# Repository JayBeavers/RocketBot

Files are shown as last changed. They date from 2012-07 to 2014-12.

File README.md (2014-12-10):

# RocketBot #


RocketBot is a project to create a robot that uses an air compressor to launch straw rockets that was demonstrated at the 2012 Maker Faires in San Mateo CA and Seattle WA.  Its journey is chronicalled at [http://jaybeavers.org](http://jaybeavers.org).

----------

## [RocketBaseArduino](https://github.com/JayBeavers/RocketBot/tree/master/RocketBaseArduino) ##

RocketBaseArduino is the source code for the Arduino that controls the robot platform that runs the rocket launcher which includes an air compressor, a pan/tilt servo for the launcher, an industrial LED warning light, and a warning speaker.

RocketBaseArduino is controlled using the [Reflecta](https://github.com/JayBeavers/Reflecta) remoting protocol.  RocketBaseArduino implements the 'RBOT1' interface which controls animations (lights and sounds), pan/tilt servos of the rocket launcher, and compressor and valves of the pneumatic system.  The PC receives a heartbeat of the current state of the robot every 200 ms.

The PC-side source code has not been published.  I've switched from a C#/XNA application to a [nodejs client](https://github.com/JayBeavers/Reflecta/tree/master/NodeClient) but the port is not yet complete.  The previous application used XBox Wireless Controller buttons to switch between animations and initiate launch and the thumb stick to drive the servos.

## [ReflectaMonsterMoto](https://github.com/JayBeavers/ReflectaMonsterMoto) ##

ReflectaMonsterMoto is the source code for the [Teensy (Arduino-compatible board)](http://www.pjrc.com/teensy/) and [SparkFun Monster Moto Shield](https://www.sparkfun.com/products/10182) system that runs the RocketBot drive train.

Like RocketBaseArduino, the PC-side source code has not been published due to a switch from C#/XNA over to nodejs.  The previous application used an XBox Wireless Controller thumbstick to control the drive train.  The logic behind this control was subject to much hacking over the course of Maker Faire as I adjusted the acceleration curve, turn rate, etc. to make the robot deftly controllable through the heavy crowds.

## [Schematics](https://github.com/JayBeavers/RocketBot/tree/master/Schematics) ##

I've uploaded the diagrams I used with a lasercutter to make the RocketBot plates.  There's also a layout of the pneumatic parts and an early draft of the power system used to enable the Arduino to control high current 12v components such as the compressor, industrial warning light, and pneumatic valves.

## [Parts List](https://github.com/JayBeavers/RocketBot/blob/master/PartsList.md) ##

List of parts used to create RocketBot.

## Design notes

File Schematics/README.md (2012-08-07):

# Hardware Schematics for RocketBot #

These are the design diagrams used to build the RocketBot prototype.

The base plate designs were created in Visio to be used on a laser cutter which had been tuned to work well with these settings (0 width lines, coloration for cut vs. raster).  These settings are different than what Ponoko wants so if you want to use that service to cut your plates some significant editing will be needed.

I loaded a few of these into AutoCAD 2013 (imports well) and InkScape (imports mostly intact).  I found Inkscape to do better with the SVG import than the dxf import so I've exported both formats.

The electronics design (.dsn file) was done using TinyCAD.  I didn't find an 'export to' in TinyCAD that was more portable so you'll need to use that app to read the file.

## Rocket Drive Base 4 ##

Base plate for the drive train for RocketBot.  I attached a Parallax drive train and two Parallax casters from an Eddie kit.  The empty front area held a Dell Mini-9 netbook running Windows 8, during the show we hotglued some straws to act as 'inside bumpers' to keep the netbook from sliding off the robot.  We added some zip ties and zip tie mounts to secure the battery.  We also found out the hard way that if you don't protect the Arduino's USB connector, hard use will strain and break the USB connection.

## Rocket Base 3 ##

Base plate for the rocket layer of RocketBot.  This was connected on top of Rocket Drive Base using the Eddie chassis spacers.  For the RTM release, we shifted the transistors down next to the air tank in order to shorten cable lengths.

We also found out the hard way that an Arduino mounted on the outside of the plate where the USB connector sticks out slightly is very bad -- at the end of the first day when I was quite tired I drove the robot into a pole on the left side and ripped off the USB connector, resulting in a hurried replacement of the Arduino from the Maker Shed.  RocketBot v2 has a laser cut 'cable holder' that takes all strain off the usb connectors.  I've also moved the Arduino (and all fragile components) inside the plate to get better crash protection.

## Rocket Electronics ##

This is a very simple diagram of the early circuits.  Much out of spec of what was finally produced.  Will rediagram for RocketBot v2.

## Pneumatic Prototype 1 ##

Layout of the pneumatic components.  In the final release I moved the analog pressure sensor to valve port 2 and removed the associated tee, otherwise pretty much unchanged.

## MARK 2 Drive Base v3 ##

A somewhat related project -- using most of the same components as RocketBot, add a centermount for an 8020 rod to make a 'human height' prototyping platform.  I did this work after seeing so many Parallax Eddies chopped up to remove their second platter and replace it with some type of height extension system.

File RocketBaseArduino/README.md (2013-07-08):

# Rocket Base Arduino #

Rocket Base Arduino exposes commands to allow a host to control the RocketBot's launch plate over the Arduino's USB or UART (Serial) port by using the Reflecta protocol via the rbot1 interface.

The commands exposed are:

- animation (id): Display a visual and audible animation sequence
    - 0: Idle
    - 1: Moving
    - 2: Arming
    - 3: Armed
    - 4: Firing
    - 5: Fired
    - 6: Moving Disabled
- fire(): Fire the rocket!
- light(val): Manually set the warning light LED bitmask (1:Red, 2:Green, 4: Blue)
- pan(angle)
- tilt(angle)
- compressor(on): '1' on, '0' off
- valve(val): '0' both off, '2' valve 2 open, '4' valve 4 open

In addition, pin A0 is hooked to the pressure sensor which can be accessed via ardu1.analogRead.

To install this library, upload sketch RocketBaseArduino to your Arduino.  Note that you must first [install the Reflecta Arduino libraries](https://github.com/JayBeavers/Reflecta#getting-started).

To call this library, use the [Reflecta Node Client](https://github.com/JayBeavers/Reflecta/tree/master/NodeClient) library.  A simple example is:

    var devicePath = "/dev/ttyACM0"; // or "COM4" et al in Windows
    var Reflecta = require('reflecta');
    var reflecta = new reflecta.Board(devicePath, function(err) {
      reflecta.rbot1.animation(4);
      reflecta.rbot1.fire();
      reflecta.rbot1.animation(5);
    });

## Release History

- 0.1.0: Initial release
- 0.1.1: Updated with changes to Reflecta and ardu1

### Future Work ###

- Convert custom heartbeat code over to Reflecta's new hart1 approach like in BasicIMU.ino
- Create an integrated nodejs sample that maps an XBox GamePad to these methods like was used at Maker Faire.
- To be reworked for Rocket Bot v2.

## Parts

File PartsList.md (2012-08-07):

# Parts List #

[Sparkfun Monster Moto Shield](https://www.sparkfun.com/products/10182), $80

2x [PJRC Teensy](http://www.pjrc.com/store/teensy.html) Arduino-compatible microcontroller, $16 ea

2x [Parallax Caster Wheel](http://www.parallax.com/Store/Robots/RoboticAccessories/tabid/145/CategoryID/22/List/0/SortField/0/Level/a/ProductID/527/Default.aspx) Kits, $43 ea

[Parallax Motor Mount and Wheel Kit](http://www.parallax.com/Store/Robots/RoboticAccessories/tabid/145/CategoryID/22/List/0/SortField/0/catpageindex/2/Level/a/ProductID/507/Default.aspx), $299

2x (45 cm x 45 cm x 1 cm) ABS plastic to cut bases, ~$12

[12.8V 6.6 Ah LiFePO4 Battery](http://www.batteryspace.com/LFP-Battery-12.8V-6.6Ah-84Wh-16A-rate-for-scuba-diving.aspx), $96

[Smart Battery Charger](http://www.batteryspace.com/smartcharger30afor128v4cellslifepo4batterypack110-240vac.aspx), $22

[FIRST 2012 Pneumatic Base Kit](http://www.andymark.com/product-p/am-2000.htm), $281

[Festo VUVG 12v Valve Pack](http://www.andymark.com/product-p/am-0888.htm), $94

[Menics MS86M Warning Light](http://www.wolfautomation.com/products/36249/86mm-led-strobe-light-3-colors-in-1brmenics-ms86m), $130

[Menics MS86 Pole Mount Adapter](http://www.wolfautomation.com/products/33066/pole-mount-adapterbrmenics-ms86-accessory-mam-ds31), $0

[Menics MAP Pole](http://www.wolfautomation.com/products/1029/poles-for-the-mam-basesbrmenics-map-pole), $5

[Servo City DDT500 Tilt](http://www.servocity.com/html/ddt500_direct_drive_tilt.html), $25

Copper launch tube & flexible tubing from local hardware store

Straws, Eraser tips, hot melt, and construction paper for rockets

Custom MOSFET power board

XBox Wireless Controller with PC Receiver

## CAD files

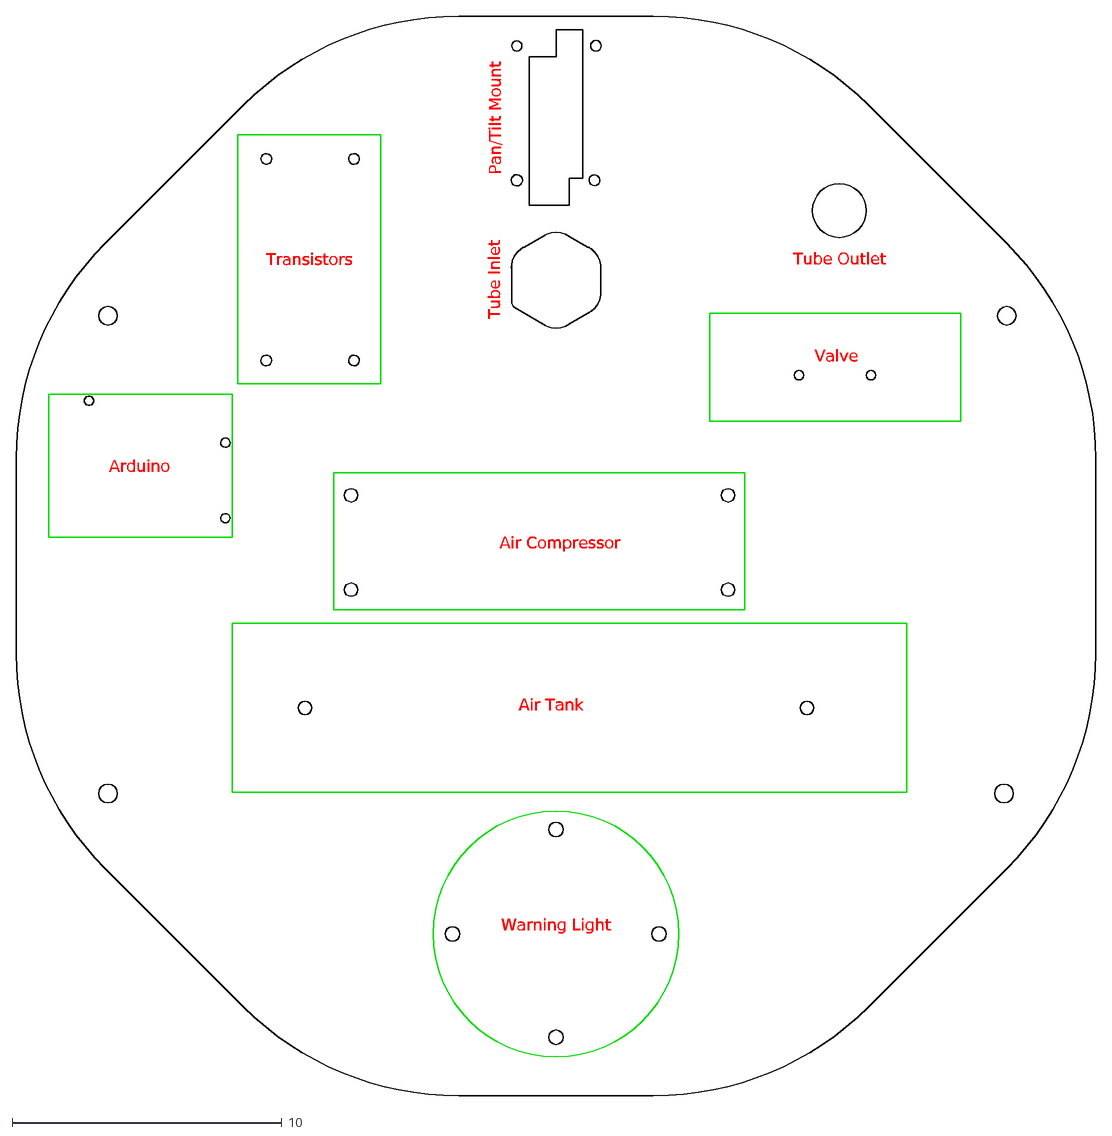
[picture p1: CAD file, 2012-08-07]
Schematics/Rocket Base 3.dxf
Pan/Tilt Mount
Tube Inlet
Air Compressor
Air Tank
Warning Light
Valve
Arduino
Transistors
Tube Outlet

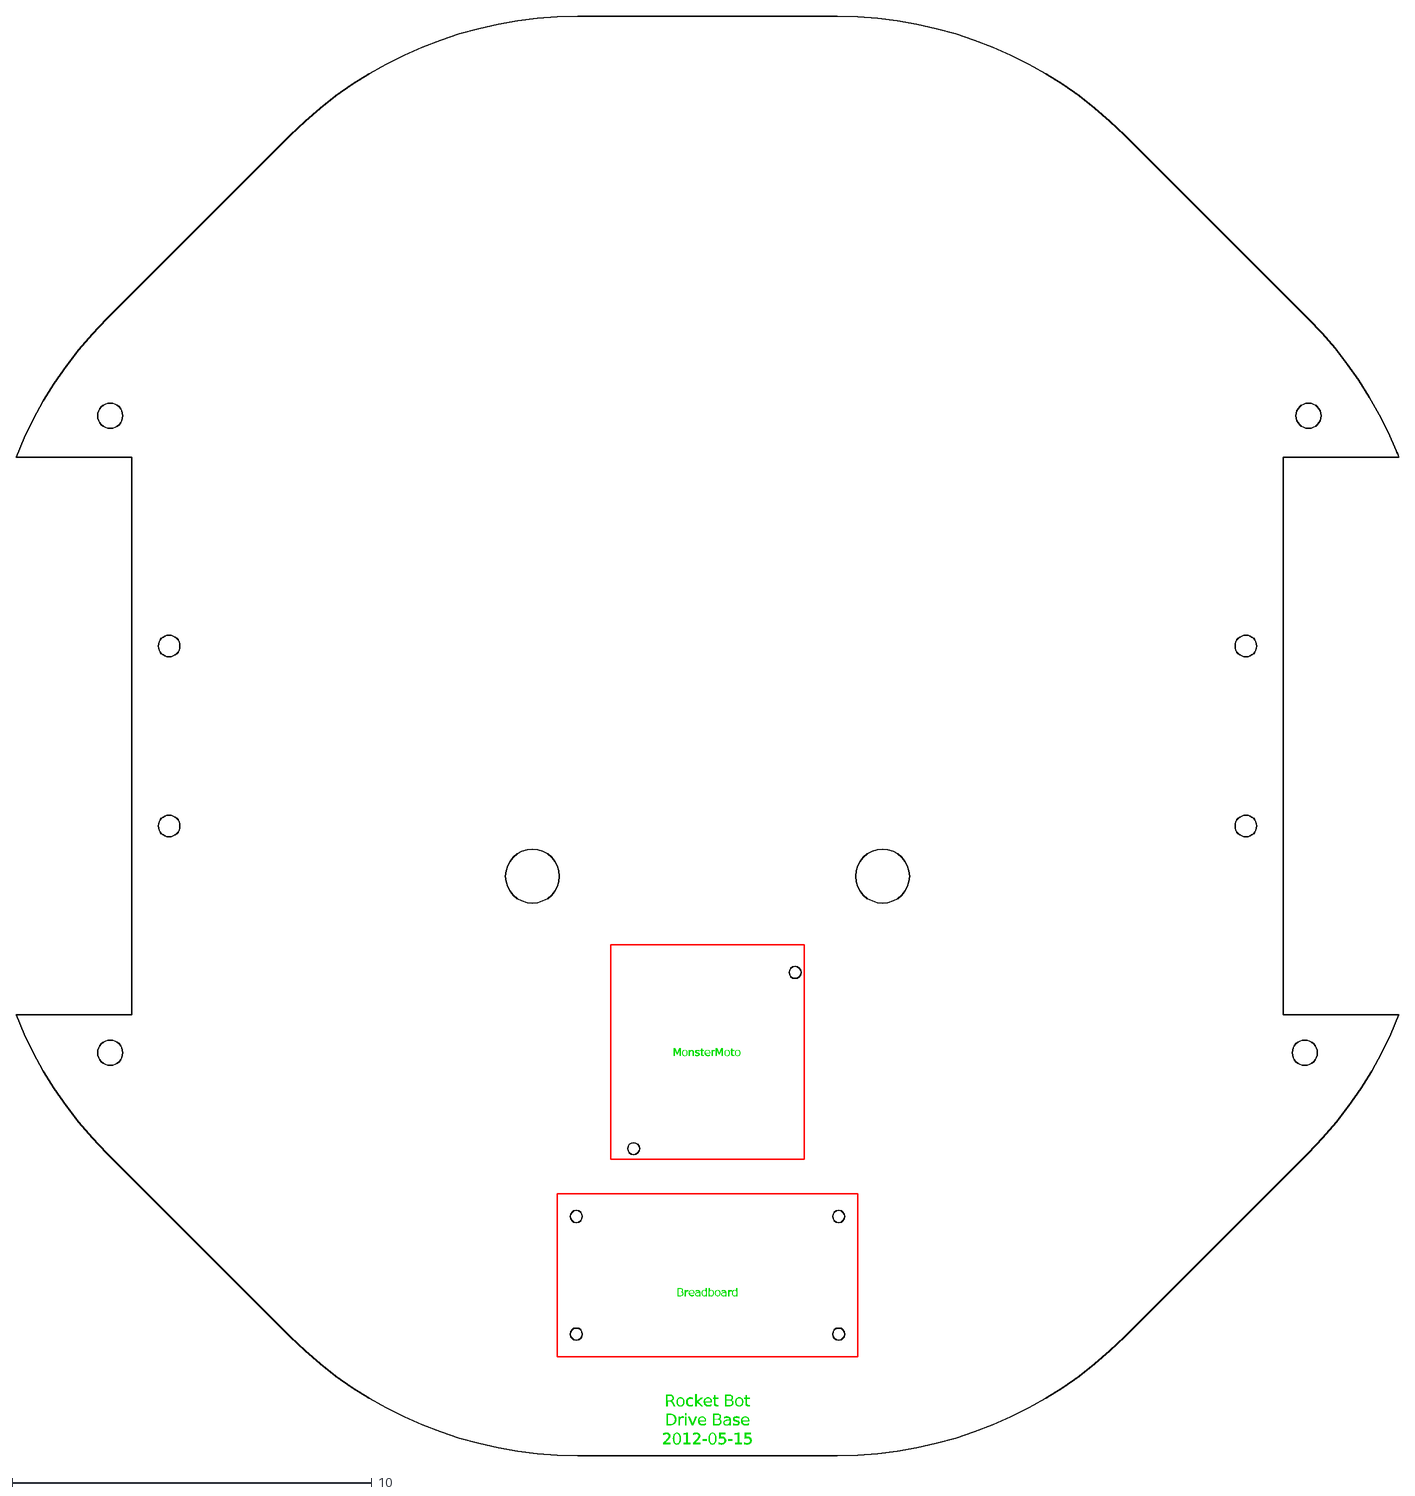
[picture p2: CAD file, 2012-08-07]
Schematics/Rocket Drive Base 4.dxf
Rocket Bot Drive Base 2012-05-15
Breadboard
MonsterMoto

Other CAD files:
Schematics/MARK 2 Drive Base v3.dxf

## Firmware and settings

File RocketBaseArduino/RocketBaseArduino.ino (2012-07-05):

#include <Arduino.h>
#include <Servo.h>
#include <ReflectaFramesSerial.h>
#include <ReflectaFunctions.h>

#define RedLight 9
#define GreenLight 10
#define BlueLight 11
#define ValveClosed 12
#define ValveOpen 13
#define Compressor 7
#define Speaker 8
#define PanServo 3
#define TiltServo 4
#define PressureSensor 0

Servo pan;
Servo tilt;

void setup() {

  pinMode(RedLight, OUTPUT);
  pinMode(GreenLight, OUTPUT);
  pinMode(BlueLight, OUTPUT);
  pinMode(ValveClosed, OUTPUT);
  pinMode(ValveOpen, OUTPUT);
  pinMode(Compressor, OUTPUT);
  pinMode(Speaker, OUTPUT);

  digitalWrite(RedLight, LOW);
  digitalWrite(GreenLight, LOW);
  digitalWrite(BlueLight, LOW);

  digitalWrite(ValveClosed, HIGH);
  digitalWrite(ValveOpen, LOW);
  digitalWrite(Compressor, LOW);

  delay(10);
  digitalWrite(ValveClosed, LOW);
 
  pan.attach(PanServo);
  tilt.attach(TiltServo);

  pan.write(90);
  tilt.write(120);
  
  reflectaFrames::setup(9600);
  reflectaFunctions::setup();
  
  reflectaFunctions::bind("RBOT1", AnimationCommand);
  reflectaFunctions::bind("RBOT1", FireCommand);
  reflectaFunctions::bind("RBOT1", LightCommand);
  reflectaFunctions::bind("RBOT1", PanCommand);
  reflectaFunctions::bind("RBOT1", TiltCommand);
  reflectaFunctions::bind("RBOT1", CompressorCommand);
  reflectaFunctions::bind("RBOT1", ValveCommand);
}

void loop(){

  reflectaFrames::loop();
  sendHeartbeat();
  animationLoop();  
  delay(5); // Delay needed for animation loop timing
}

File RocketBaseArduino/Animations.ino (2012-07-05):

unsigned long animationStart = 0;
unsigned long animationTime = 0;
int frequency = 0;

typedef void (* AnimationFunction) ();
AnimationFunction animation = IdleAnimation;

void animationLoop()
{
  animationTime = millis() - animationStart;
  animation();
}

int AnimationCommandState()
{
  if (animation == IdleAnimation) return 0;
  else if (animation == MovingAnimation) return 1;
  else if (animation == ArmingAnimation) return 2;
  else if (animation == ArmedAnimation) return 3;
  else if (animation == FiringAnimation) return 4;
  else if (animation == FiredAnimation) return 5;
}

void AnimationCommand()
{
  switch(reflectaFunctions::pop())
  {
    case '0':
      animation = IdleAnimation;
      break;
    case '1':
      animation = MovingAnimation;
      break;
    case '2':
      animation = ArmingAnimation;
      break;
    case '3':
      animation = ArmedAnimation;
      break;
    case '4':
      animation = FiringAnimation;
      break;
    case '5':
      animation = FiredAnimation;
      break;
    case '6':
      animation = MovingDisabledAnimation;
      break;
  }
  
  // Reset to defaults
  digitalWrite(RedLight, LOW);
  digitalWrite(GreenLight, LOW);
  digitalWrite(BlueLight, LOW);
  frequency = 0;
  animationStart = millis();
}

void IdleAnimation()
{
  frequency = 0;
  noTone(Speaker);
  animationStart = millis();
}

void MovingAnimation()
{
  if (animationTime < 150)
  {
    tone(Speaker, 660);
    digitalWrite(RedLight, HIGH);
    digitalWrite(GreenLight, HIGH);
    digitalWrite(BlueLight, HIGH);
  }

  else if (animationTime < 1000)
  {
    noTone(Speaker);
    digitalWrite(RedLight, LOW);
    digitalWrite(GreenLight, LOW);
    digitalWrite(BlueLight, LOW);
  }
  else
  {
    animationStart = millis();
  }
}

void MovingDisabledAnimation()
{
  if (animationTime < 150)
  {
    tone(Speaker, 660);
    digitalWrite(RedLight, HIGH);
    digitalWrite(GreenLight, HIGH);
    digitalWrite(BlueLight, LOW);
  }

  else if (animationTime < 1000)
  {
    noTone(Speaker);
    digitalWrite(RedLight, LOW);
    digitalWrite(GreenLight, LOW);
    digitalWrite(BlueLight, LOW);
  }
  else
  {
    animationStart = millis();
  }
}

void ArmingAnimation()
{
  if (frequency == 0)
  {
    digitalWrite(RedLight, HIGH);
    digitalWrite(GreenLight, HIGH);
    digitalWrite(BlueLight, LOW);
    frequency = 222;
  }
  else if (animationTime < 1250) frequency += 1;
  else if (animationTime < 1500)
  {
    digitalWrite(RedLight, LOW);
    digitalWrite(GreenLight, LOW);
    digitalWrite(BlueLight, LOW);
    frequency = 465;
  }
  else if (animationTime < 1700) frequency -= 6;
  else if (animationTime < 2000) frequency = -1; // Off
  else
  {
    frequency = 0;
    animationStart = millis();
  }
  
  if (frequency > 0)
    tone(Speaker, frequency);
  else
    noTone(Speaker);
}

void ArmedAnimation(){

  noTone(Speaker);

  if (animationTime < 4000)
  {
    digitalWrite(RedLight, HIGH);
    digitalWrite(GreenLight, HIGH);
    digitalWrite(BlueLight, LOW);
  }
  else if (animationTime < 8000)
  {
    digitalWrite(RedLight, LOW);
    digitalWrite(GreenLight, LOW);
    digitalWrite(BlueLight, LOW);
  }
  else
  {
    animationStart = millis();
  }
}

void FiringAnimation()
{
  if (frequency == 0)
  {
    frequency = 215;
  }
  else if (animationTime < 75)
  {
    digitalWrite(RedLight, HIGH);
    digitalWrite(GreenLight, LOW);
    digitalWrite(BlueLight, LOW);
    frequency += 5;
  }
  else if (animationTime < 325)
  {
    digitalWrite(RedLight, LOW);
    digitalWrite(GreenLight, LOW);
    digitalWrite(BlueLight, LOW);
    frequency = 290;
  }
  else if (animationTime < 400)
  {
    digitalWrite(RedLight, HIGH);
    digitalWrite(GreenLight, LOW);
    digitalWrite(BlueLight, LOW);
    frequency -= 5;
  }
  else if (animationTime < 650)
  {
    digitalWrite(RedLight, LOW);
    digitalWrite(GreenLight, LOW);
    digitalWrite(BlueLight, LOW);
    frequency = 215;
  }
  else if (animationTime < 725)
  {
    digitalWrite(RedLight, HIGH);
    digitalWrite(GreenLight, LOW);
    digitalWrite(BlueLight, LOW);
    frequency += 5;
  }
  else if (animationTime < 975)
  {
    digitalWrite(RedLight, LOW);
    digitalWrite(GreenLight, LOW);
    digitalWrite(BlueLight, LOW);
    frequency = 290;
  }
  else if (animationTime < 1050)
  {
    digitalWrite(RedLight, HIGH);
    digitalWrite(GreenLight, LOW);
    digitalWrite(BlueLight, LOW);
    frequency -= 5;
  }
  else if (animationTime < 1300)
  {
    digitalWrite(RedLight, LOW);
    digitalWrite(GreenLight, LOW);
    digitalWrite(BlueLight, LOW);
    frequency = 215;
  }
  else
  {
    animation = IdleAnimation;
  }
  
  if (frequency > 0)
    tone(Speaker, frequency);
  else
    noTone(Speaker);
}

void FiredAnimation()
{
  if (animationTime < 100) digitalWrite(RedLight, HIGH);
  else if (animationTime < 200) digitalWrite(RedLight, LOW);
  else if (animationTime < 300) digitalWrite(RedLight, HIGH);
  else if (animationTime < 400) digitalWrite(RedLight, LOW);
  else if (animationTime < 500) digitalWrite(RedLight, HIGH);
  else if (animationTime < 600) digitalWrite(RedLight, LOW);
  else if (animationTime < 700) digitalWrite(RedLight, HIGH);
  else
  {
    digitalWrite(RedLight, LOW);
    
    animation = IdleAnimation;
  }
}

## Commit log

2012-07-03 Rename MakerFaire.ino to RocketbaseArduino.ino to match folder name per Arduino IDE needs
2012-07-05 Conversion of RocketBot over to Reflecta
    Removed custom remote procedure call protocol, replaced with Reflecta
    bindings.
    [Animations.ino, Commands.ino, RocketBaseArduino.ino]
2012-07-06 Initial commit of drive base source, using a Teensy to drive a Sparkfun MonsterMoto board via Reflecta
2012-08-07 Adding schematics for RocketBot's base plates
    [MARK 2 Drive Base v3.dxf, Rocket Base 3.dxf, Rocket Drive Base 4.dxf]
2012-08-07 Early draft diagrams from the design process
    [Rocket Electronics.dsn]
2012-08-07 Readme for the schematics
2012-08-14 Adding ARDU1 to DriveBase firmware, enable motors by default, move to int16 power.
